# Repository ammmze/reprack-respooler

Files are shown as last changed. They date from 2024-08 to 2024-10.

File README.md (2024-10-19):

# Reprack Re-spooler

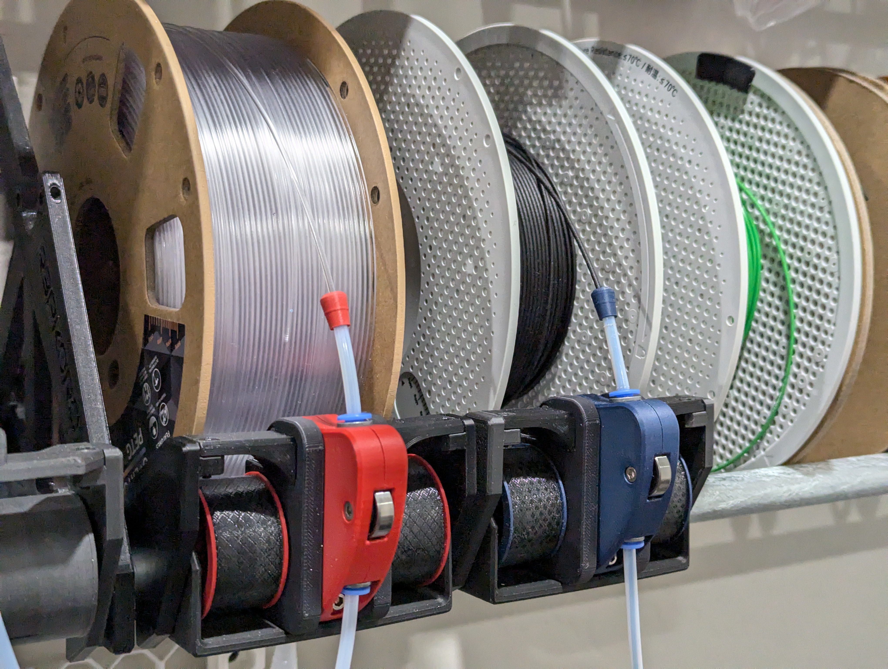
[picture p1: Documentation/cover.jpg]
cover


This re-spooler works on the general principal that the 
[Filamentalist](https://github.com/Enraged-Rabbit-Community/ERCF_v2/tree/master/Recommended_Options/Filamentalist_Rewinder)
project uses but is adapted to work with the ["Auto-Rewind Spool Holder for RepRack"](https://www.printables.com/model/292276-auto-rewind-spool-holder-for-reprack) and some inspiration take from the re-spooler in the [8-track project](https://github.com/ArmoredTurtle/8-Track-Raven-Alpha/tree/main).

## Goals / Challenges to overcome

There are some challenges with using Filamentalist on the Reprack that required something a little different.

### Roller wheel size

Due to the position of the conduit pipe that is core to the Reprack, using the larger wheels that Filamentalist uses
is not really feasible. However, these larger wheels are important to the rewinding ratio to ensure that even on near
empty spools, it rewinds fast enough for a tight wind. So we need smaller and faster rollers.

To combat this, the drive wheel (the wheel with the o-rings, driven by filament being pushed) is not directly attached to the
roller shaft, but is instead positioned next to the roller shaft. This allows us to apply a gear ratio of roughly 1:2, making the
roller shaft spin about twice the speed of the drive wheel.

### Direction of feed

The standard filamentalist feeds filament from the bottom of the spool and out the front. This is rather inconvenient to load a
spool when there are other shelves above it. When used in a wall mounted Reprack, feeding from the front of the spool, going downward
is more convenient.

The solution for the roller wheel size also makes way for the direction of feed as well. Effectively we need the roller shaft to spin
in the opposite direction of the drive wheel. By having the drive wheel mesh with roller shaft rather than having an axial connection,
the directions are reversed.

## Documentation

See [Documentation](./Documentation/README.md).

## Potential issues

I think the main potential issue I imagine running into with this is perhaps the longevity of the o-rings. I don't think tension on the filament when the wind is tight is enough to completely disengage the o-rings, so I suspect the filament drags across the o-rings and will slowly wear them out.

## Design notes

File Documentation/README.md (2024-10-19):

# Documentation

## Bill of Materials / BOM

### Printed parts

| Name | Quantity | Notes |
| --- | --- | --- |
| Spool holder frame | 1 | Use the "Main parts" > "Frame.3mf" from [here](https://www.printables.com/model/292276-auto-rewind-spool-holder-for-reprack/files). You can omit the one cross member piece that has a long slot for the filament. The re-spooler has an replacement for that. |
| Rear roller | 1 | Use  the "Main parts" > "Cylinder Shell.3mf" from [here](https://www.printables.com/model/292276-auto-rewind-spool-holder-for-reprack/files). You only need 1 of these for this application, NOT 2. And you do NOT need the coils either. |
| [Drive wheel - for 608 bearing](./STL/Drive%20wheel%20-%20for%20608%20bearing.stl) | 1 | |
| [Drive wheel bearing adapter](./STL/Drive%20wheel%20bearing%20adapter.stl) | 1 | |
| [Drum](./STL/Drum%20x2.stl) | 2 | |
| [Frame front cross member left](./STL/Frame%20front%20cross%20member%20left.stl) | 1 | |
| [Frame front cross member right](./STL/Frame%20front%20cross%20member%20right.stl) | 1 | |
| [Frame](./STL/Frame.stl) | 1 | |
| [Inner Shoulder](./STL/Inner%20Shoulder%20x2.stl) | 2 | |
| [R4 bearing idler adapter](./STL/R4%20bearing%20idler%20adapter.stl) | 1 | Only needed if using an R4 bearing for the idle bearing instead of a 625 bearing. May want to enable "detect thin walls", which seemed to have the slicer do it in a single wall rather than like 1.5 walls. |
| [Re-spooler sled](./STL/Re-spooler%20sled.stl) | 1 | |
| [Roller Grip](./STL/Roller%20Grip.stl) | 1 | |
| [Sleeve TPU](./STL/Sleeve%20TPU%20x2.stl) | 2 | |
| [Tension Arm Left](./STL/Tension%20Arm%20Left.stl) | 1 | |
| [Tension Arm Right](./STL/Tension%20Arm%20Right.stl) | 1 | |
| [Tension nut](./STL/Tension%20nut.stl) | 1 | |
| [PTFE Feeder](./STL/PTFE%20Feeder.stl) | 1 | |

> [!NOTE]
> My parts are currently printed with PLA using the following settings:
> * 0.2mm layer height
> * 0.4mm nozzle
> * 2 walls
> * 15% infill

### Hardware

| Name | Quantity | Notes |
| --- | --- | --- |
| 608 Bearings | 5 | 2 used in each shaft and one in the drive wheel. May be a bit excessive, but it's a common and cheap bearing. |
| 625 or R4 bearing | 1 | Be sure to print R4 adapter if using R4 bearing. No extra adapter needed for 625, it fits directly in the tension arm. |
| #211 O-rings | 2 | 13/16" ID, 1 1/16" OD |
| M3 heat insert | 5 | Voron standard 5mm OD, 4mm L |
| Spring from BMG extruder kit | 1 | 6mm OD, 1mm wire, 15mm free length |
| M3 nut | 8 | Main spool holder frame |
| M3 x 6mm Socket head cap screw | 1 | Fastens re-spooler to sled |
| M3 x 8mm Socket head cap screw | 8 | Main spool holder frame |
| M3 x 12mm Socket head cap screw | 2 | Fastens tension arm halves |
| M3 x 25mm Socket head cap screw | 1 | Pivot for tension arm |
| M3 x 30mm Socket head cap screw | 1 | Tension screw |
| One-way bearing | 1 | 8mm bore, 12mm Length, 14mm Diameter, Octagon shape |
| 8mm x 80mm metal rod | 1 | Main shaft for respooler |
| 40mm PTFE tube | 1 | 4mm OD x 2.5mm or 3mm ID |

> [!NOTE]
> The above BOM includes the hardware needed for the spool holder frame from the original project.

## Assembly

### Spool holder frame

First assemble the spool holder frame and rear cylinder (minus the spring coil) using the instructions provided [here](https://www.printables.com/model/292276-auto-rewind-spool-holder-for-reprack). It's easy...just insert some M3 nuts and M3 x 8mm screws, toss in a couple 608 bearings and screw the cap on the cylinder. And omit the upper-front piece, the re-spooler has a replacement cross member.

### Re-spooler

1. Insert heat set inserts (1 in tension nut, 2 in tension arm, and 1 in side of frame, 1 in bottom of frame)
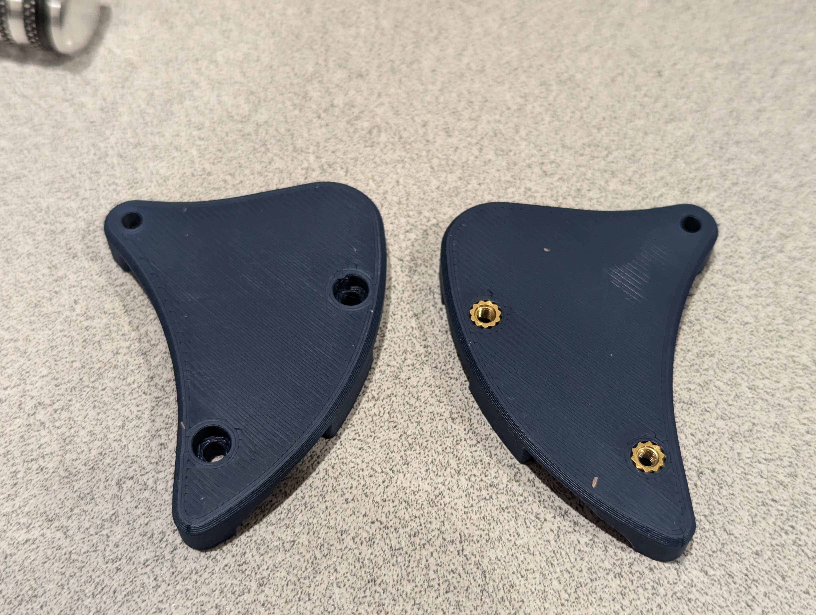
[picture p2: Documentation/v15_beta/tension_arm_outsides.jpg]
tension arm heat inserts
   
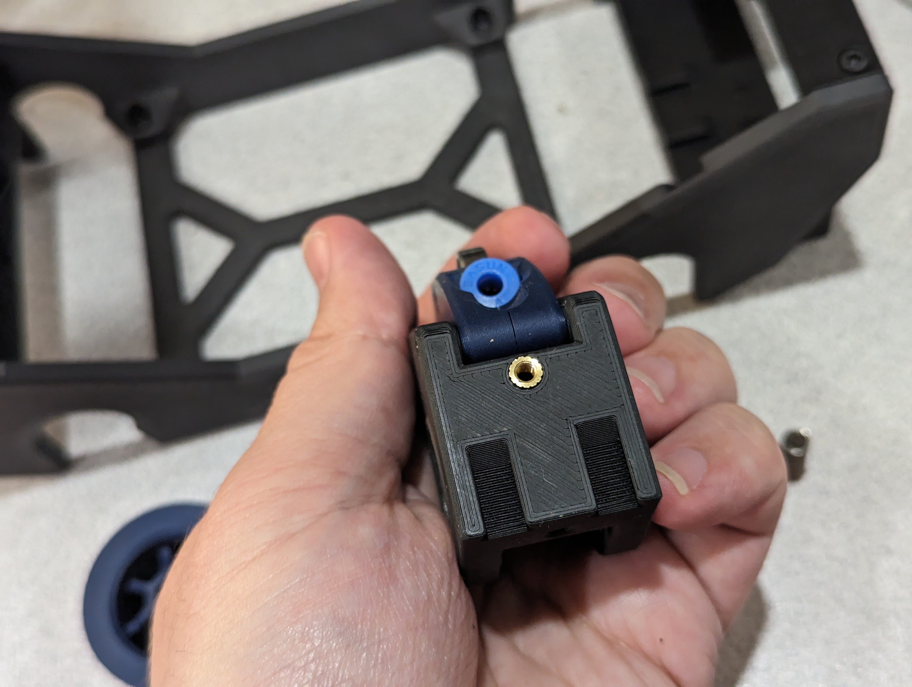
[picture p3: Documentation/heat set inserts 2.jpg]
frame heat insert
   
2. Assemble ECAS04 Collets, remove the rubber seal (it won't be used). I find it easiest to install the latch (typically blue in most ECAS) by placing the body in the tension arm, then close up the tension arm and use it as a tool to grip the ECAS body and press the latch in. Then take it out and do the other one. 
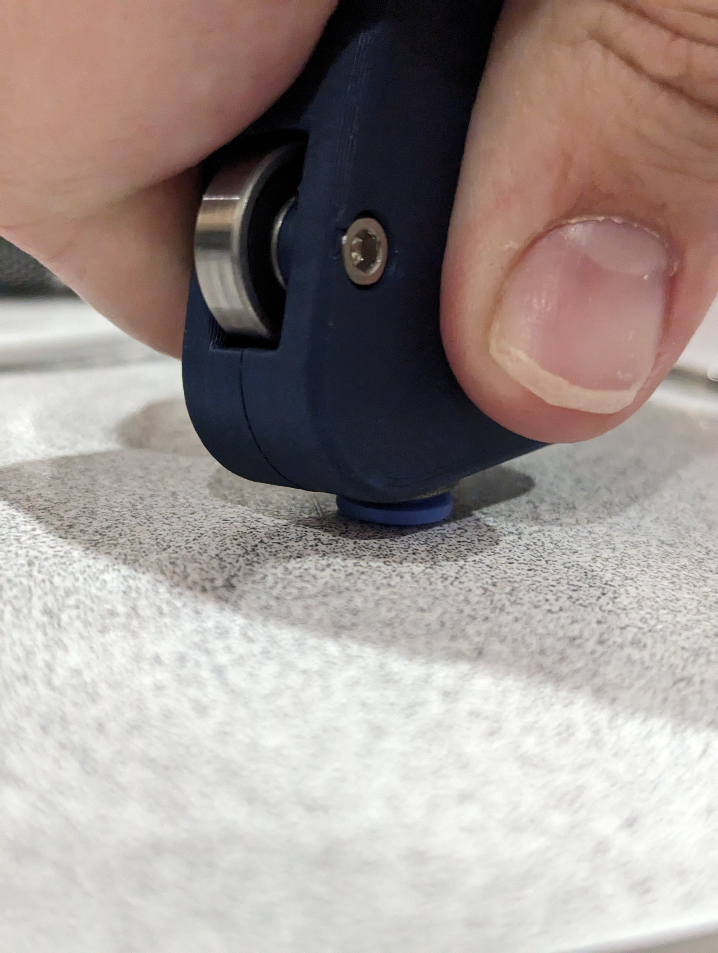
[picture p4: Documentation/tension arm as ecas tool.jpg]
tension arm as ecas tool

3. Assemble the drive wheel (see [image](./drive%20wheel%20assembly.jpg)). Insert 608 bearing into drive wheel, then insert drive wheel adapter to the center of the 608 bearing. Note this adapter is slotted. This allows the drive wheel to slide back and forth as part of the tensioning mechanism.
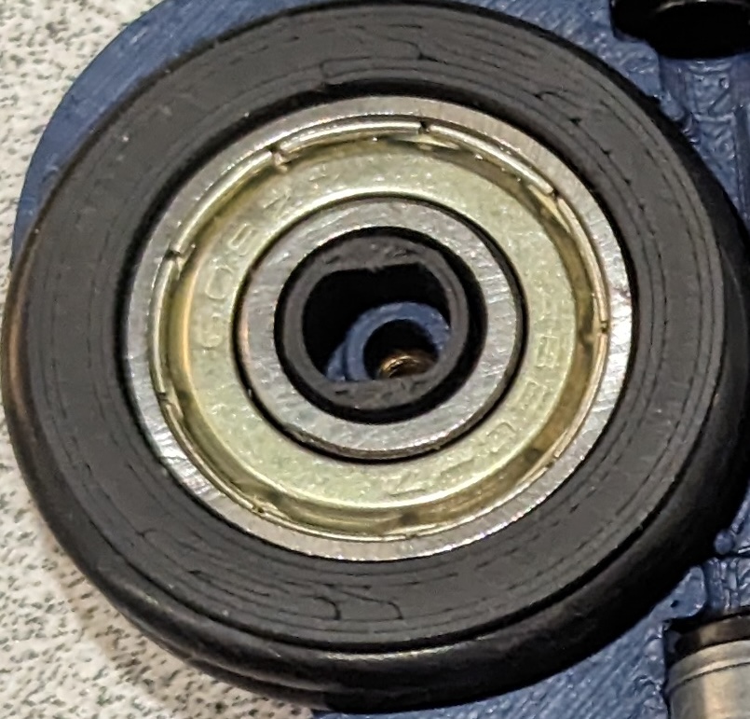
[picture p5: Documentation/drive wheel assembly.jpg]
drive wheel
   
4. Add idle bearing, drive wheel, and ECAS collets to the tension arm. The idle bearing can use either a 625 bearing directly, or an R4 bearing with the small adapter ring. Finish up the tension arm by putting the 2 halves together and fasten with 2 12mm screws. See [this](./tension%20arm%20assembly.jpg) photo of an earlier revision that shows the R4 bearing with the adapter (thin red part in middle of the bearing)
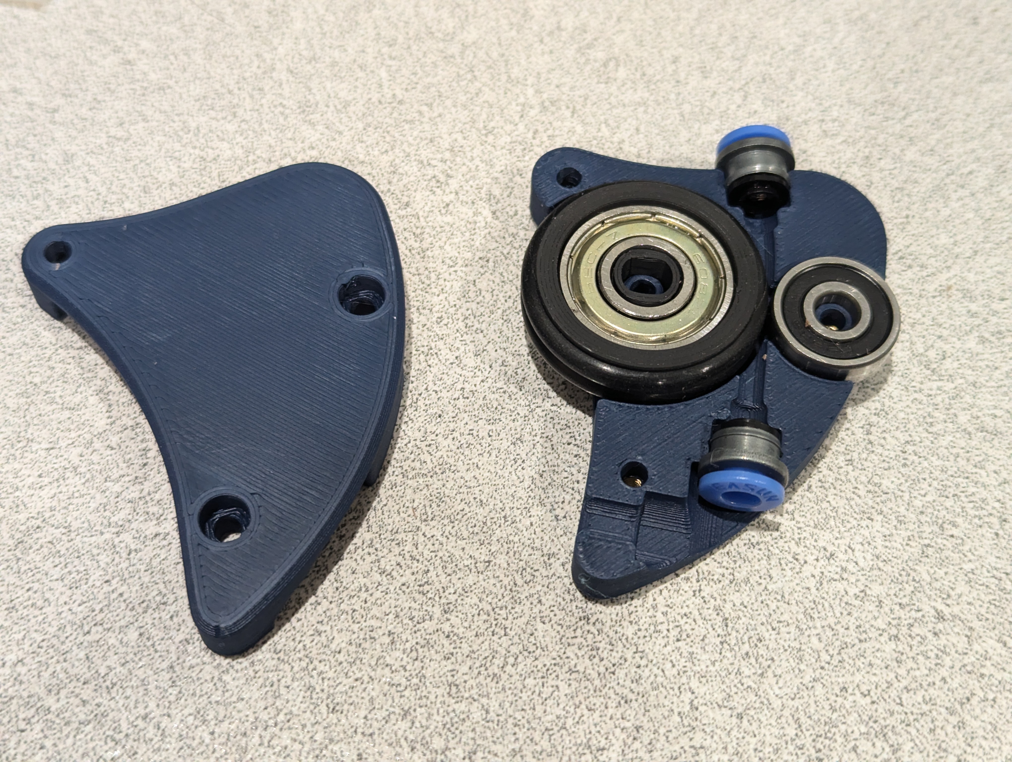
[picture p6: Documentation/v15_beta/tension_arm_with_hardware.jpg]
tension arm with hardware

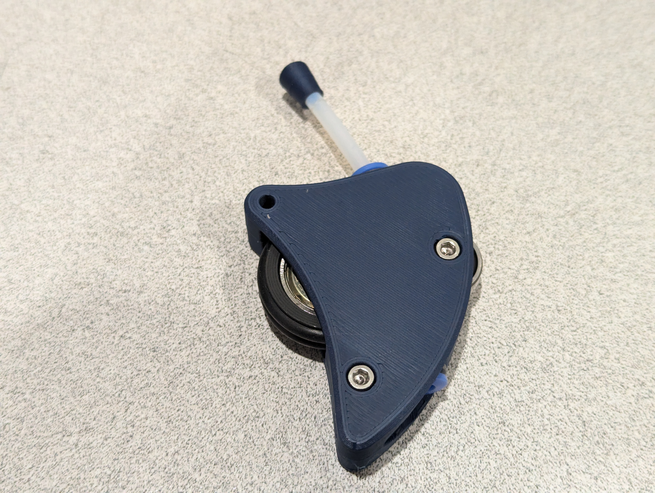
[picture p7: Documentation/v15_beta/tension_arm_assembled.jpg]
tension arm assembled

5. Insert the tension nut into the slot in the re-spooler frame, followed by the spring. It is recommened the heat insert is toward the back of the respooler, so the tension screw is pulling it through the tension nut, not out of it. See [image](./tension%20nut%20and%20spring.jpg).
6. Insert one way bearing into the "Roller Grip" and slide it onto the 8mm shaft. Then figure out which way it spins freely and which way it locks. When looking at the left side of the respooler, you want it to lock when spinning clockwise and it should spin freely when going counter clockwise. The following photo shows the orientation of the bearing relative to the frame (note the arrow on the one way bearing)
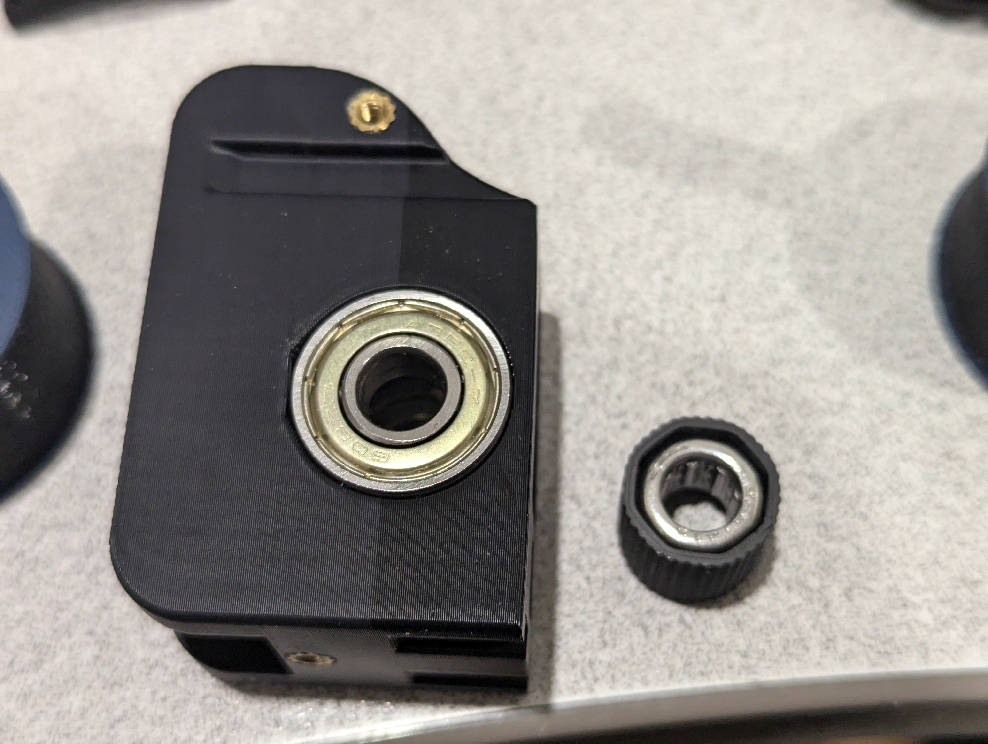
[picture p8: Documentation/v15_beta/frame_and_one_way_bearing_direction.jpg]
bearing direction

7. Insert 1 608 bearing into the respooler frame, followed by the shaft with the one way bearing, and finally the last 608 bearing.
8. Assemble the roller drums. These are slightly tapered in an attempt to help keep the spool from wandering (though it didn't really help). Slide the TPU sleeve onto the roller drum then screw on the inner shoulder. Finally slide them onto either end of the shaft. Make sure they aren't pinching the frame or friction will be too much.
9. Place the tension arm into place and put 25mm screw through the pivot hole on the top
10. Install tension screw from the front-bottom of the tension arm, back through the spring and into the tension nut. Optionally you can toss an M3 washer on this tension spring for better distribution of load.
11. Slide the sled into the spool holder frame and attach the cross member pieces using 8mm screws. 
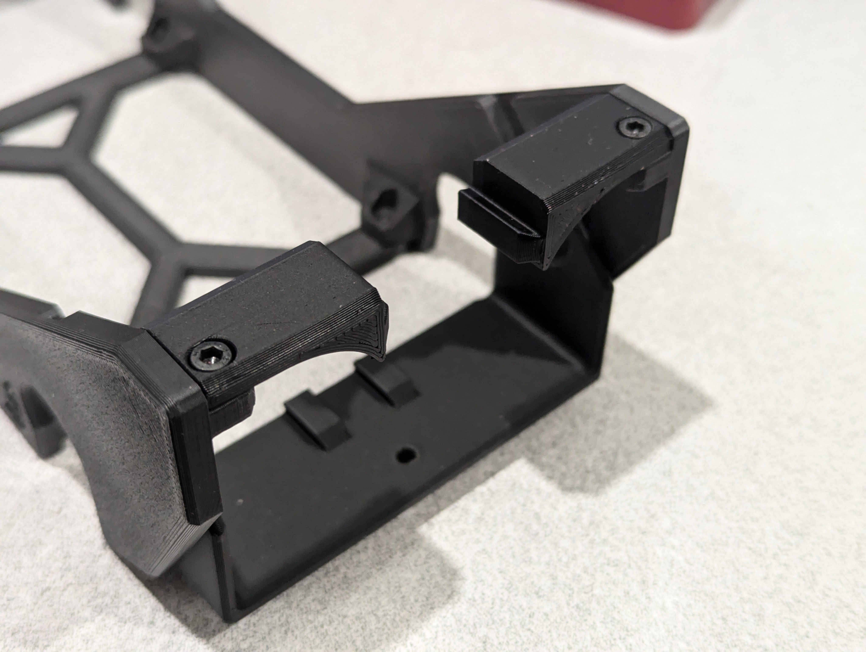
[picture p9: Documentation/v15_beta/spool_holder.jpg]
   
12. Slide the respooler in from the front and insert 6mm srew in the bottom to lock it into place. See [image](./final%20lock%20screw.jpg)

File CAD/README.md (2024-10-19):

# Reprack Respooler CAD

Original CAD files available on OnShape. [Latest version v15 (Beta)](https://cad.onshape.com/documents/1811ccbb3ce132861916e0ed/v/ac04b61fa50d85d06f1a087e/e/1f88f6f653a48f707a61aca3)

Step file available at [Reprack Rewinder Assebled v15 (Beta).step](./Reprack%20Rewinder%20Assembled%20v15%28Beta%29.step)

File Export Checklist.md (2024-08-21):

# Export Checklist

Checklist of things to be done to export/publish the project.

* Create new version in OnShape, and update the link in [CAD](./CAD/README.md).
* Export the "Reprack Rewinder Assembled" assembly from OnShape as STEP and place in the [CAD](./CAD/) directory.
* Export all the parts from the "Re-spooler/v2/Export" part studio as STL with the following settings and place them in the [STL](./STL/) directory.
  * Units: Millimeter
  * Resolution: Fine
  * Export unique parts as individual files: Checked
* Remove the "Export - " prefix from the STL files (`rename --subst 'Export - ' '' *.stl`)

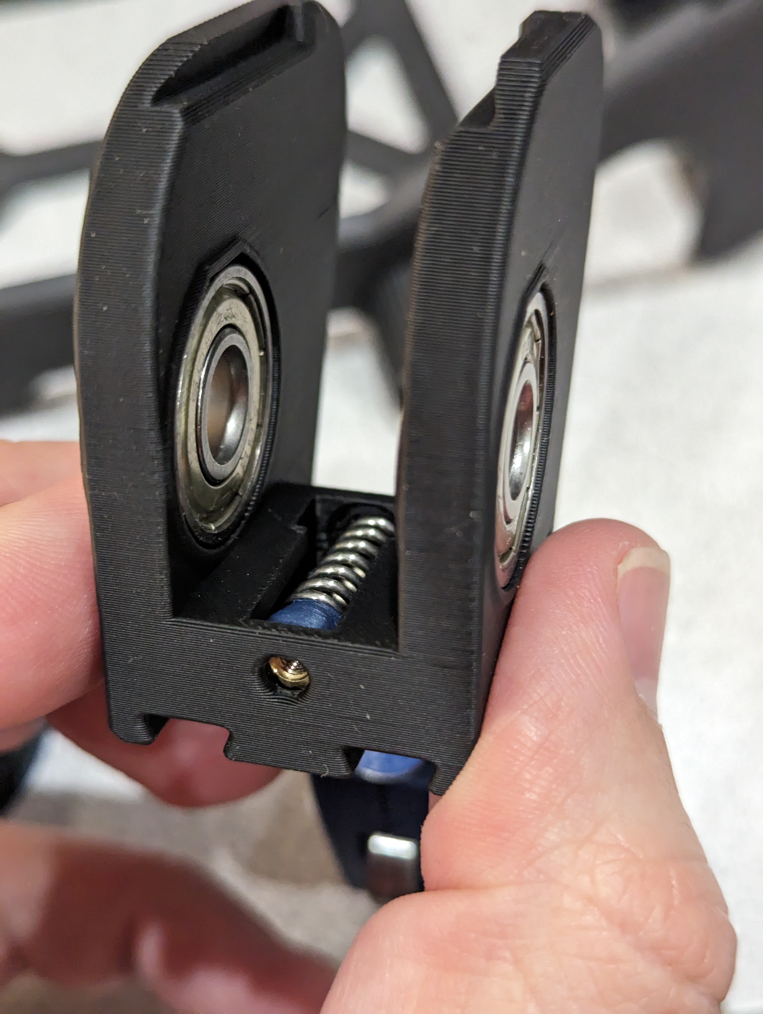
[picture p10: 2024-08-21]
Documentation/tension nut and spring.jpg

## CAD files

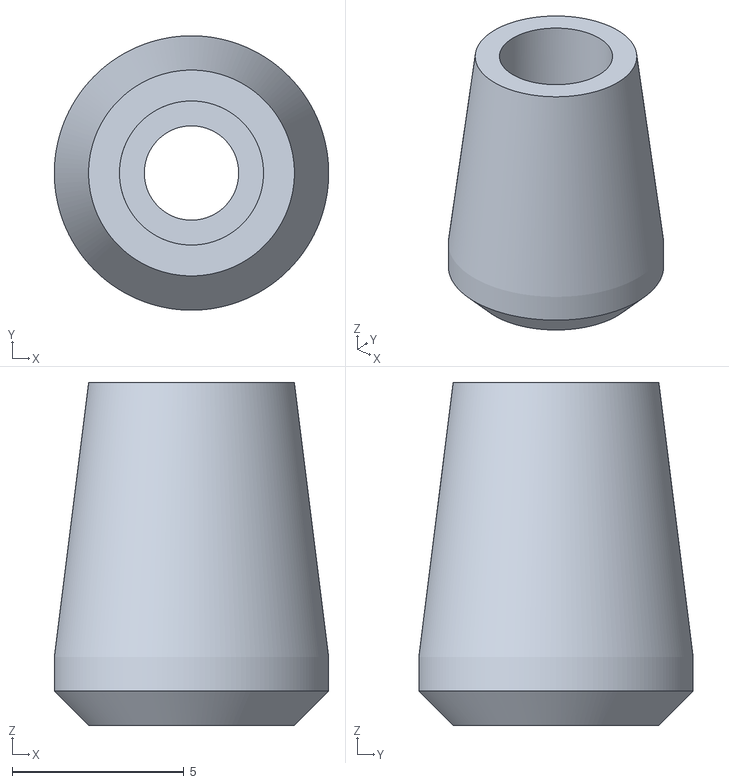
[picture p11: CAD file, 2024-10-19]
STL/PTFE Feeder.stl
8.00 x 8.00 x 10.0

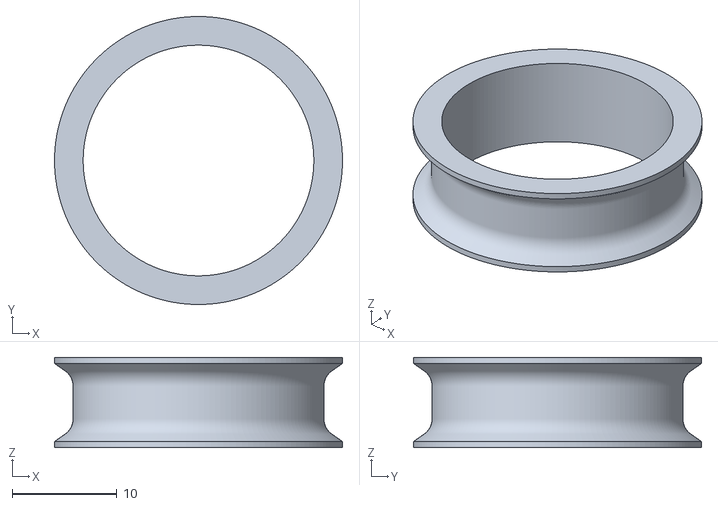
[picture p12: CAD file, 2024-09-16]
STL/Drive wheel - for 608 bearing.stl
27.5 x 27.5 x 8.60

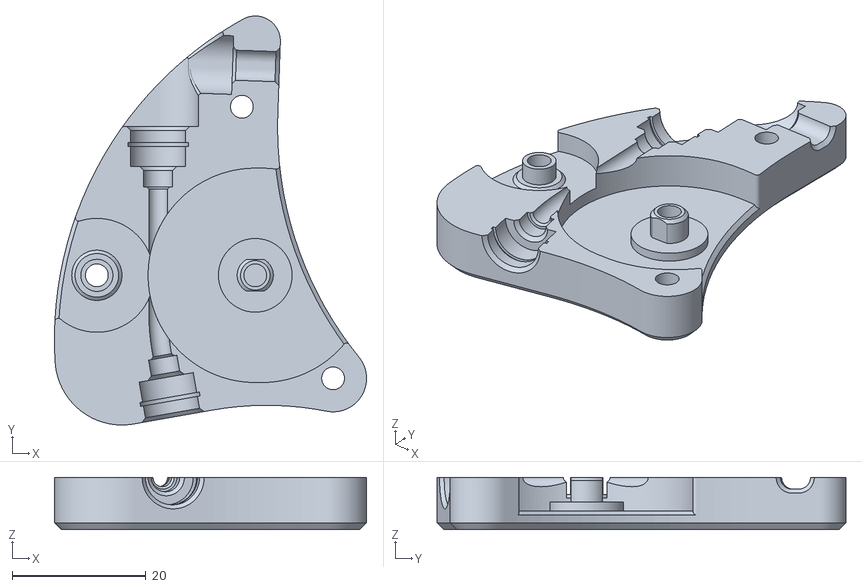
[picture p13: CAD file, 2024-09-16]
STL/Tension Arm Right.stl
46.6 x 61.1 x 7.80

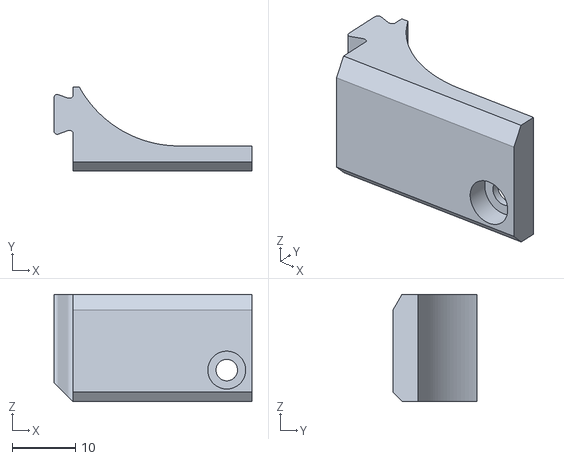
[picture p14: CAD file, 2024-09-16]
STL/Frame front cross member right.stl
31.4 x 13.4 x 17.0

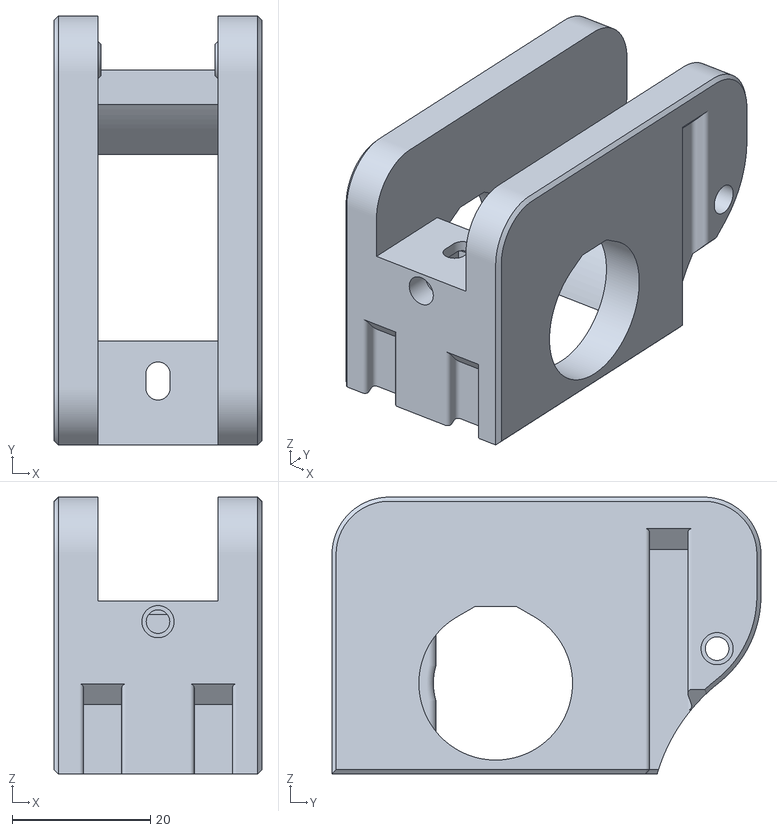
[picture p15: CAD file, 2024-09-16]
STL/Frame.stl
30.0 x 62.0 x 40.0

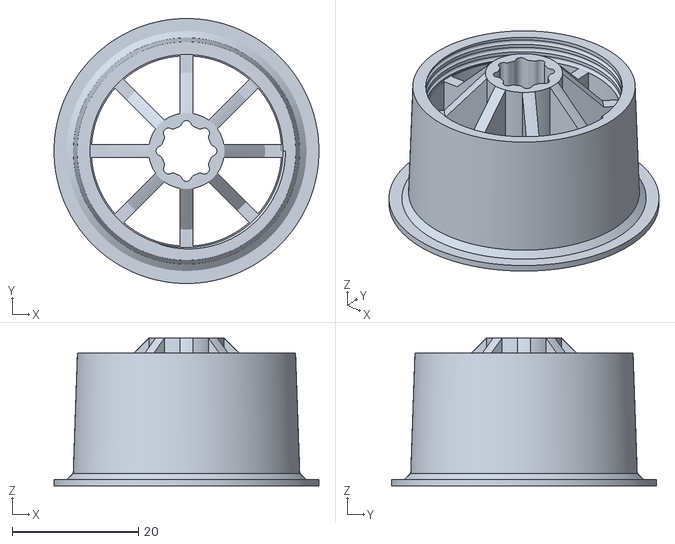
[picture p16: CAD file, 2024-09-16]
STL/Drum x2.stl
41.9 x 41.9 x 23.4

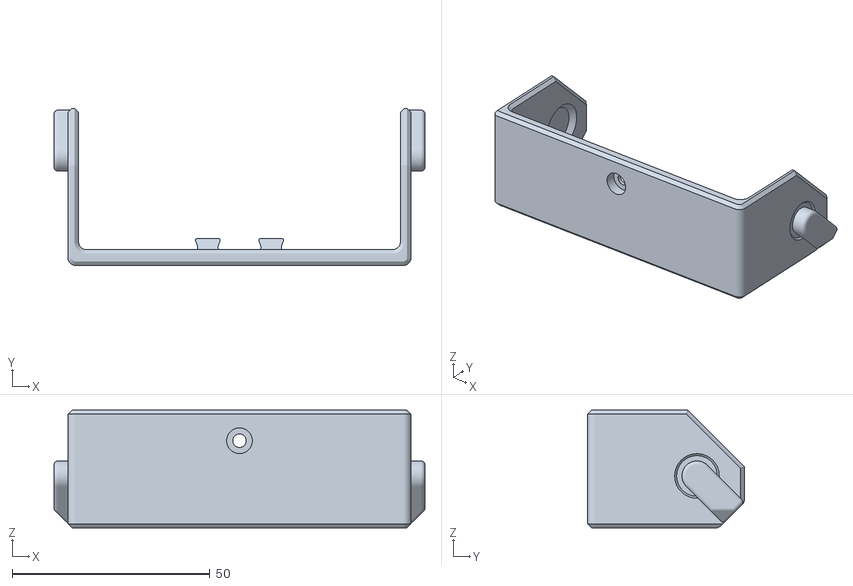
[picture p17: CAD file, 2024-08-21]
STL/Re-spooler sled.stl
93.8 x 39.7 x 29.7

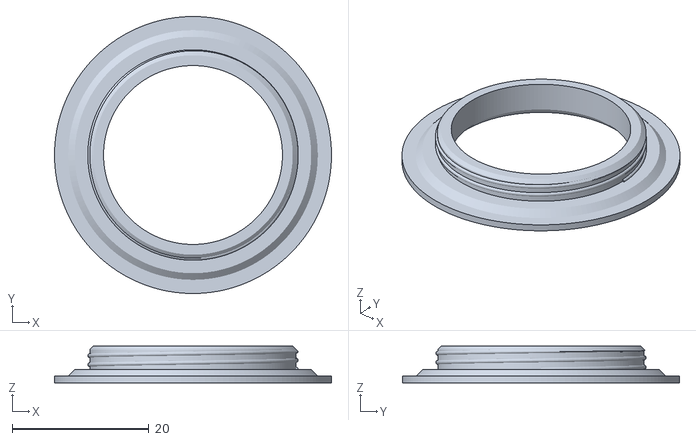
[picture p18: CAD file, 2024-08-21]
STL/Inner Shoulder x2.stl
40.4 x 40.4 x 5.40

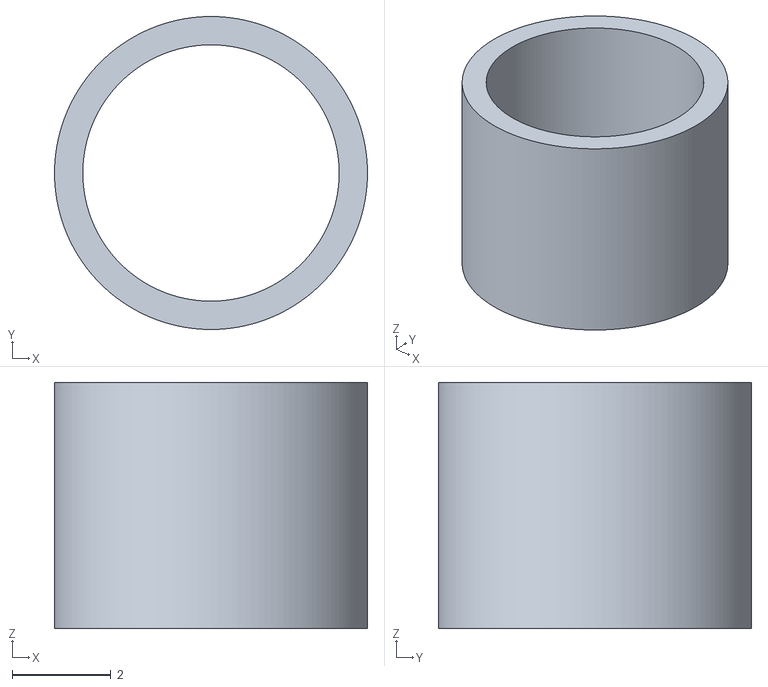
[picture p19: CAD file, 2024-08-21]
STL/R4 bearing idler adapter (if using R4 bearing).stl
6.35 x 6.35 x 5.00

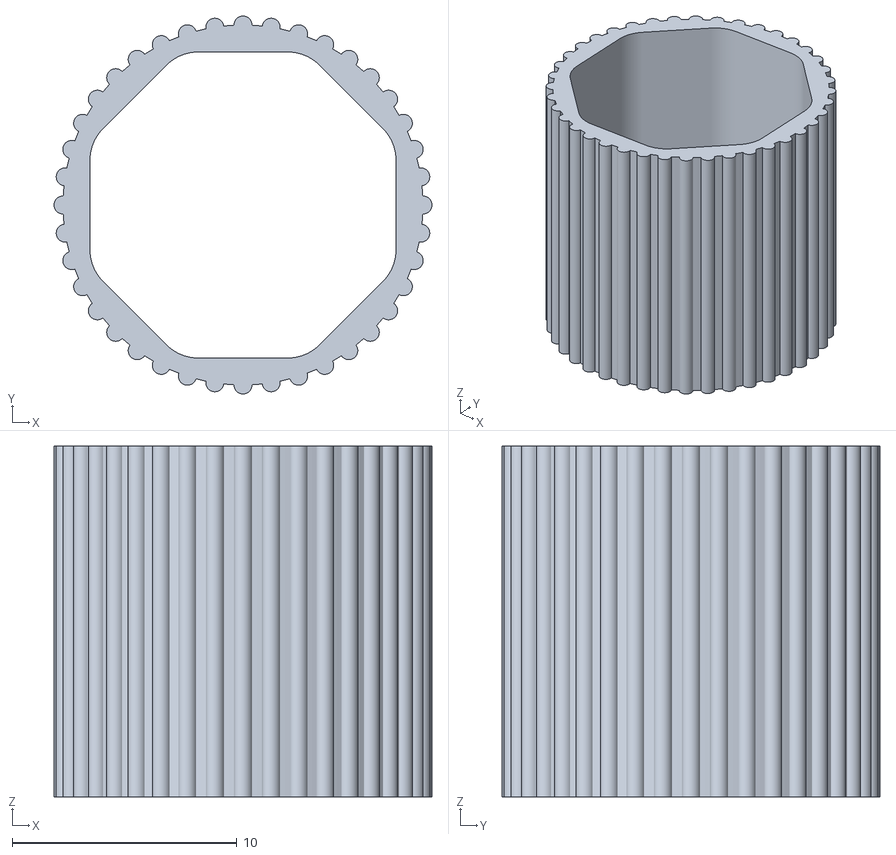
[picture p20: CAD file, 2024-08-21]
STL/Roller Grip.stl
16.8 x 16.8 x 15.6

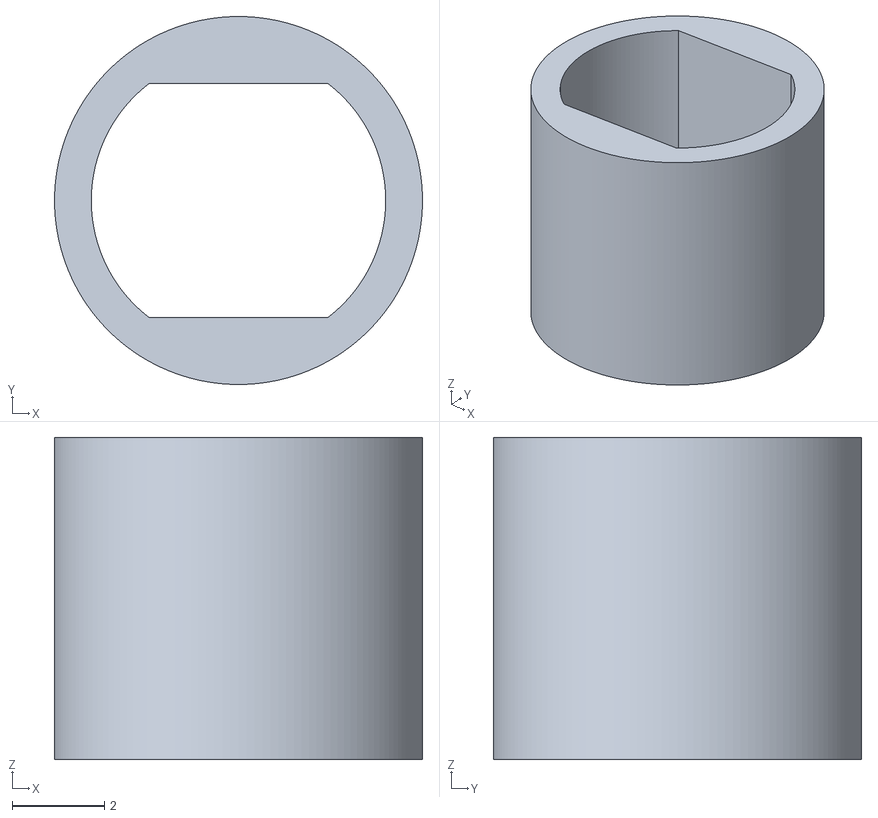
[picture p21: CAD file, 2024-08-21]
STL/Drive wheel bearing adapter.stl
8.00 x 8.00 x 7.00

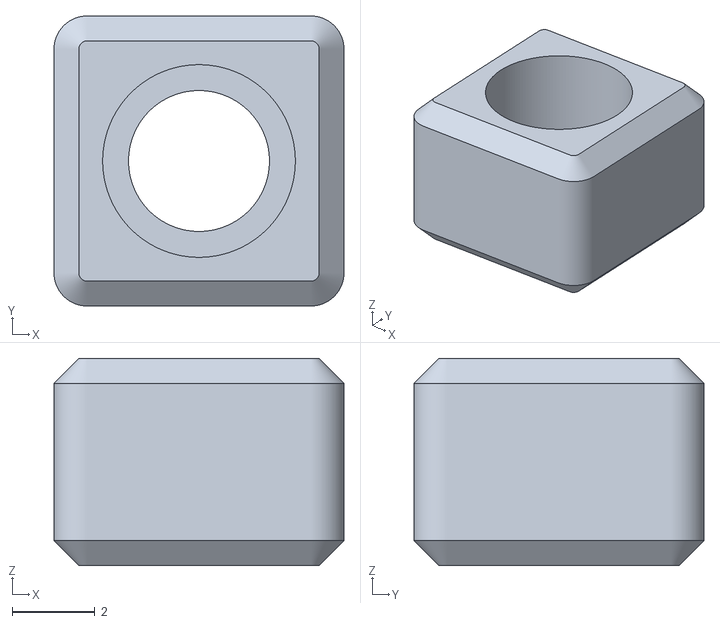
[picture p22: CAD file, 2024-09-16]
STL/Tension nut.stl
7.00 x 7.00 x 5.00

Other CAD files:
STL/Tension Arm Left.stl
STL/Frame front cross member left.stl

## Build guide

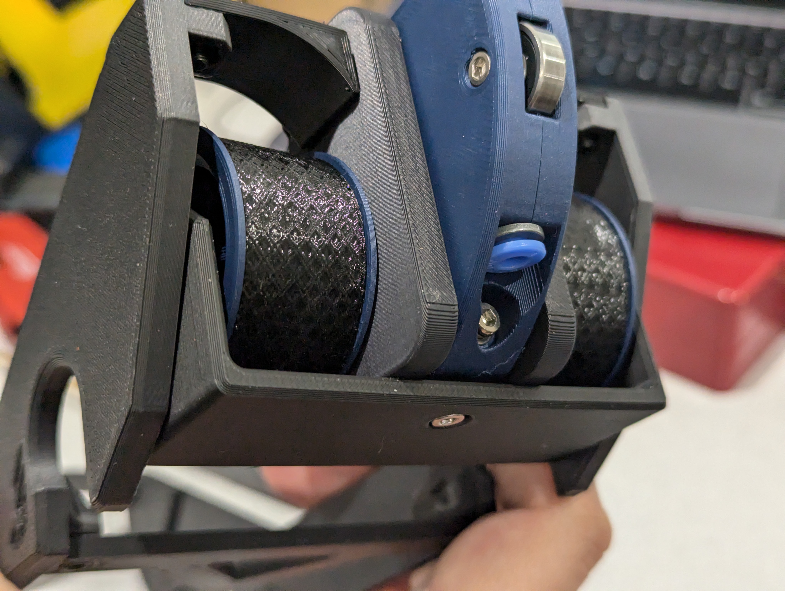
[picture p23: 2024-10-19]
Documentation/v15_beta/respooler_assembled_on_holder.jpg

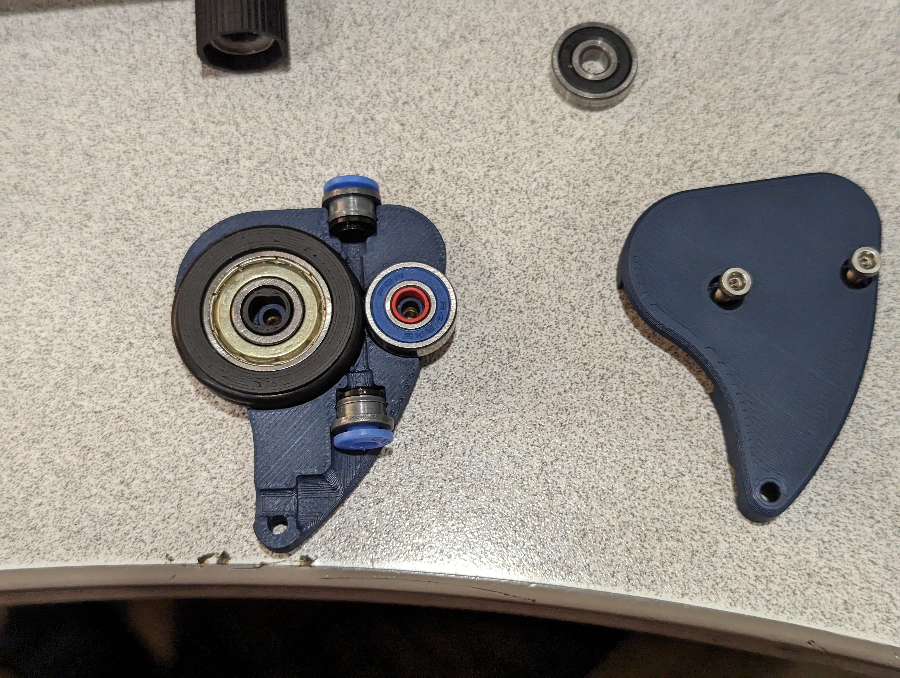
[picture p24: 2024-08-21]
Documentation/tension arm assembly.jpg

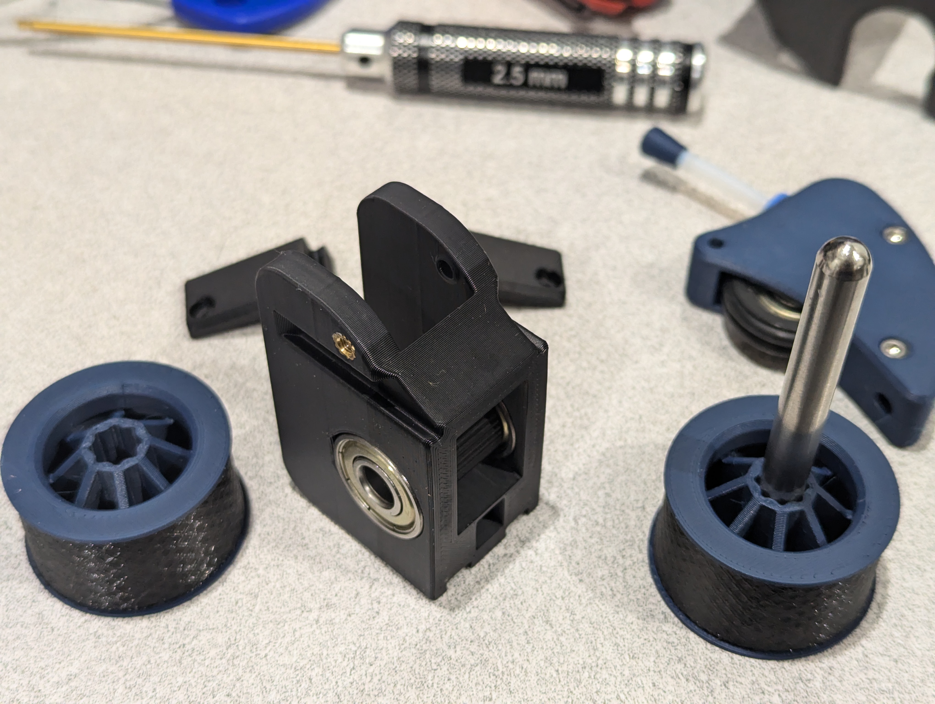
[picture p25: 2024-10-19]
Documentation/v15_beta/roller_partial_assembled.jpg

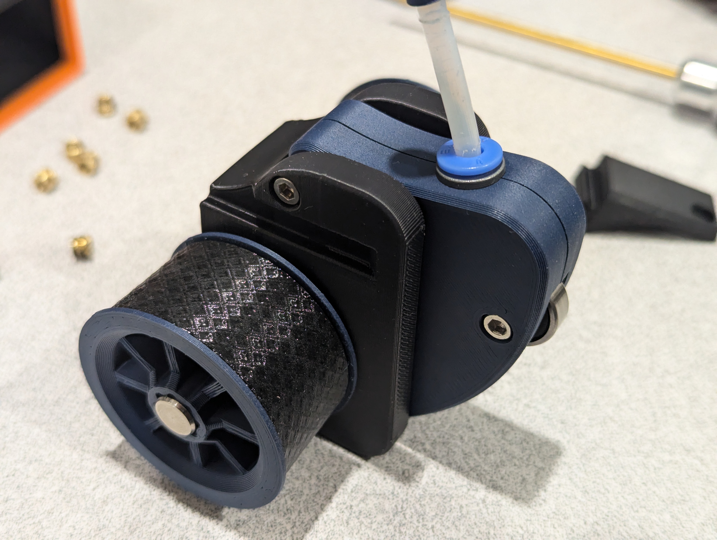
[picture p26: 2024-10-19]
Documentation/v15_beta/respooler_assembled.jpg

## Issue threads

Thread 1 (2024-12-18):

Inner Shoulder x2.stl

chadakenn, 2024-12-18:
Inner Shoulder x2.stl need sized up its a little small and wont screw in

chadakenn, 2024-12-18:
or i guess Drum x2.stl might need scaled down ill have to print the tpu tire and see

ammmze, 2024-12-22:
Looks like I have a 0.2mm clearance on there. Perhaps I should add a slight taper so that starts with a 0.2mm clearance and then reduces to 0.1 or 0.15. That should allow it to wedge in a little as you screw it in.

chadakenn, 2024-12-22:
> Looks like I have a 0.2mm clearance on there. Perhaps I should add a slight taper so that starts with a 0.2mm clearance and then reduces to 0.1 or 0.15. That should allow it to wedge in a little as you screw it in.

I never got to print the tpu as my print isn't tuned 100% for you yet so I skipped the wheels so I'm not 100%sure what part is off.... I'm starting a 2ed one and even the slicer could have sliced it wrong so I'll print each one individually and see what happens

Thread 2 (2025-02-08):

Back idler assembly missing?

piotrb, 2025-02-08:
Hey,

Just trying to figure out how this all assembles, the CAD seems to just have a rod at the back, where am I supposed to get the back roller from?

piotrb, 2025-02-08:
Or is this designed for the filamentalist idler roller to slip on top of it?

piotrb, 2025-02-10:
Never mind, saw the instructions on github :)

Closed 2025-02-10.

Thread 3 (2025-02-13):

Drum grip on shaft

piotrb, 2025-02-13:
Hey,

Love this mod :)

I'm having a bit of an issue with the drum actually gripping properly on the 8mm shaft.

Filametrix uses screws to add additional grip on their drums, would something similar be possible?

Right now I jammed a bit of TPU between them, not ideal, but at least it helps, heck if this was the official way, and the drum shaft "corners" were a little a bit bigger to actually fit some filament, it may be enough, but screws could work well too, given the tire is over the drum, it seems like it wouldn't be a big deal if there was a few slots for screws underneath gripping the shaft.

Thoughts?

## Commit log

2024-08-21 feat: initial version
    [Drive wheel - for 608 bearing.stl, Drive wheel bearing adapter.stl, Drum x2.stl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]
2024-09-16 feat: rework the arm so pivot is on top so it no longer increases tension when it should be slipping
    [Drive wheel - for 608 bearing.stl, Drum x2.stl, Frame front cross member left.stl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]
2024-10-19 feat: update for v15 (beta)
    [PTFE Feeder.stl]
2024-10-19 docs: note print settings used and potential issues around o-ring longevity
